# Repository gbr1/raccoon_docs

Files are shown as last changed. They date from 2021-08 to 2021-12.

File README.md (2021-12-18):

# Documentation and "how to" of UP Raccoon robot



# 

UP Raccoon is an AMR designed in collaboration with AAEON - UP.  This robot is completely opensource and easy to build.

## Software

Check this [guide](Raccoon&#32;robot&#32;setup.md)

## Assembly

Check the [manual assembly](assembly_manual/0_bill_of_materials.md)

## Learn more

Check these [diagrams](Raccoon&#32;robot&#32;diagrams.md)

## Events

Maker Faire Rome live [video](https://www.youtube.com/watch?v=H5PWxFA-pxc) (ita/eng)

## Demo

Check this [guide](./demo_units_docs/How%20to%20use%20the%20demo.md)

---

> ***Copyright © 2021 G. Bruno gbr1.github.io under MIT license***

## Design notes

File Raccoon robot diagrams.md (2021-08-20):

# Raccoon robot diagrams

## Hardware

Robot works on a 3S LiPo battery.

Following is how devices are powered.

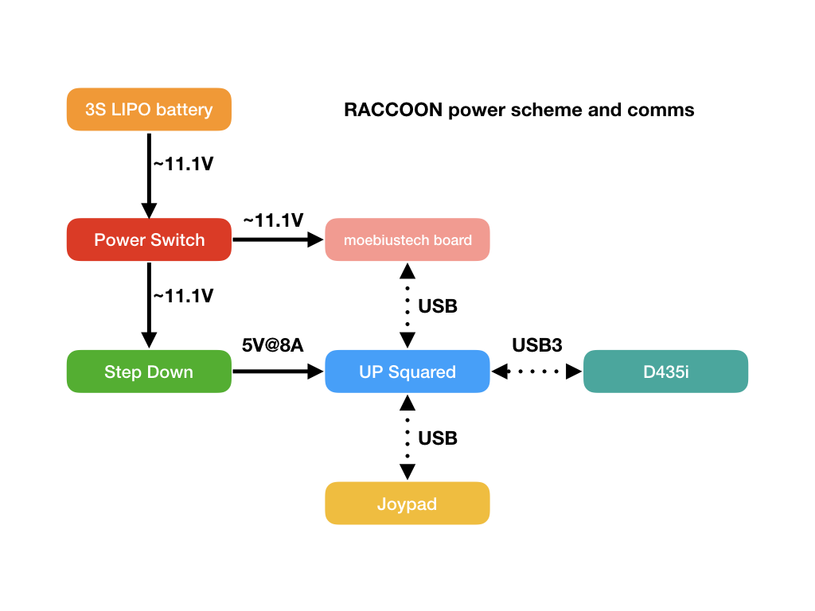
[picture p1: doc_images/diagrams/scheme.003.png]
power scheme Power diagram


## Software

The demo version works on ROS1. Check the following diagrams to take a look at involved nodes and packages.

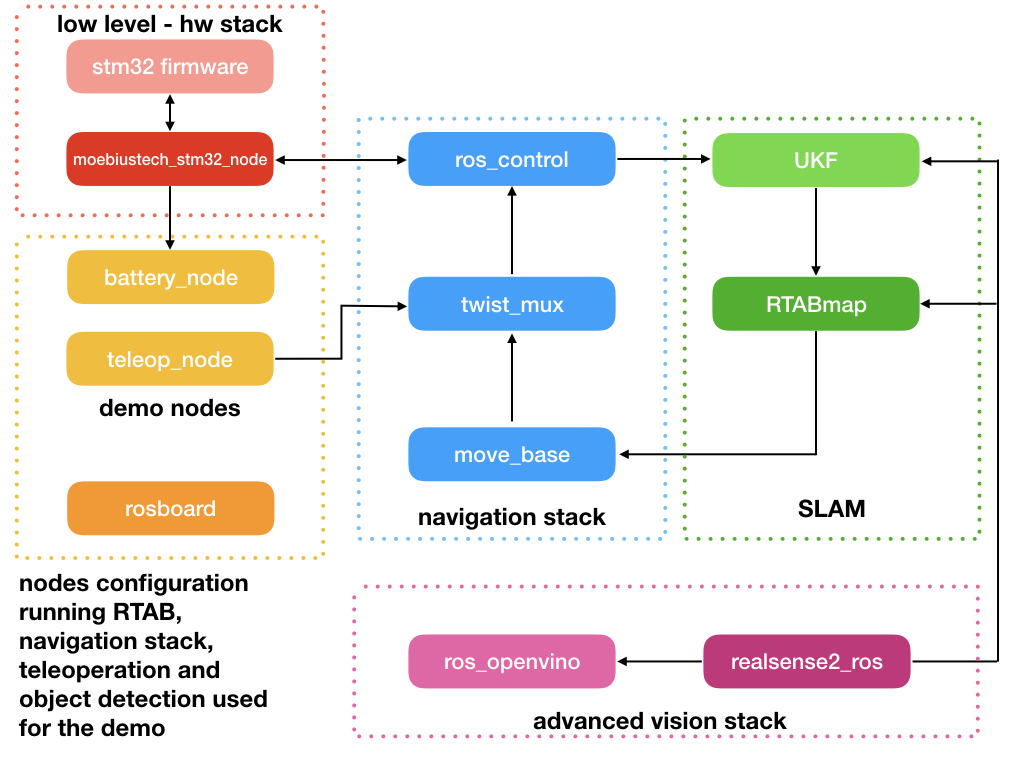
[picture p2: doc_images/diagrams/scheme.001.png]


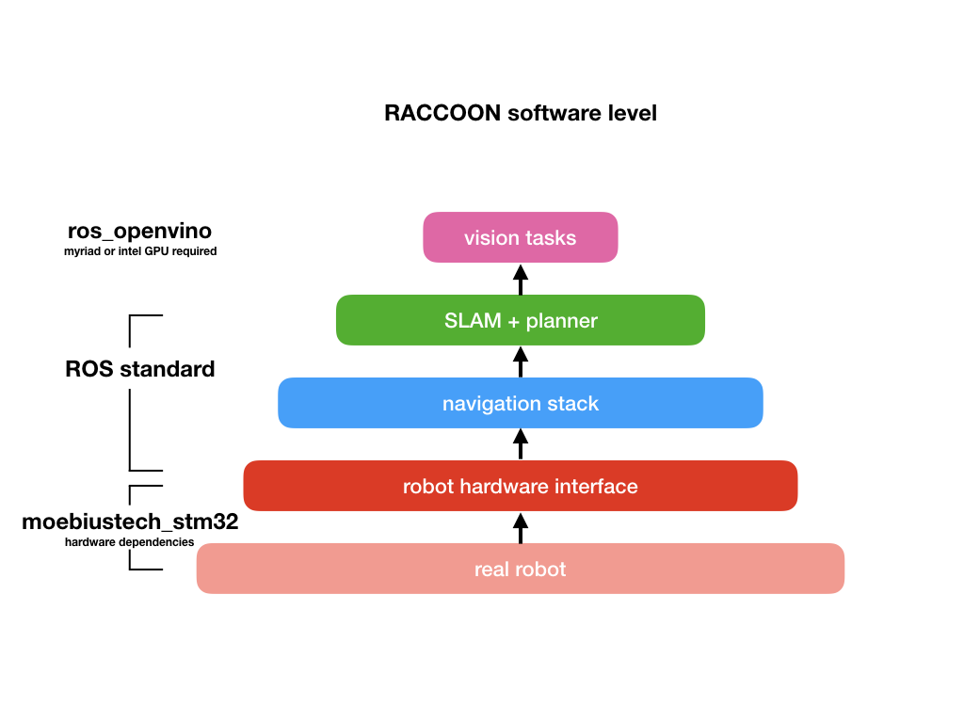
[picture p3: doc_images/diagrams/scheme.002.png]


> ***Copyright © 2021 G. Bruno gbr1.github.io under MIT license***

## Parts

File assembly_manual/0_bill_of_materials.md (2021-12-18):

# Bill of Materials

# 

### 1. Electronics & Electromechanicals

| id  | Part | Description | Qty |
| --- | --- | --- | --- |
| E01 | AAEON UP2 | UP Squared sbc | 1 |
| E02 | Wifi kit | WiFi card with antennas (PCB+SMA) | 1 |
| E03 | AAEON AI Core X | Myriad X module in PCI-e format | 1 |
| E04 | Moebiustech STM32 rosboard | A ROS board based on STM32F103RC | 1 |
| E05 | DCDC | A buck converter that can power UP2 from 12V | 1 |
| E06 | Intel Realsense D435i | Intel Realsense D435i | 1 |
| E07 | Gearmotor JGB37-520 | 12V 30:1 Gearmotor with encoder | 2 |
| E08 | Gearmotor cable | Gearmotor cable with JST connectors | 2 |
| E09 | Power switch | A round switch with red/black cables | 1 |
| E10 | Power Jack | 5.5-2.1 jack with 25cm red/black cable | 1 |
| E11 | 22AWG Cable | A 50cm red/black cable | 1 |
| E12 | USB C cable | USB 3.0 <-> USB C cable | 1 |
| E13 | USB micro cable | USB 2.0 <-> micro USB cable | 1 |
| E14 | DEANS cable | a red/black cable with DEANS connector | 1 |
| E15 | Mammoth connector | 3 vias mammout connector (3 vias) | 1 |

### 2. Mechanicals

| id  | Part | Description | Qty |
| --- | --- | --- | --- |
| M01 | M2.5x20+6 | Standoffs with M2.5 mounts, 20mm with 6mm screw | 4 |
| M02 | M3x30+6 | Standoffs with M3 mounts, 30mm with 6mm screw | 4 |
| M03 | M2.5 nut | M2.5 nuts | 22  |
| M04 | M3 nut | M3 nuts | 12  |
| M05 | M2.5x6 | M2.5 screw of 6mm lenght | 18  |
| M06 | M2.5x14 | M2.5 screw of 14mm lenght | 4 |
| M07 | M3x5 | M3 screw of 5mm lenght | 12  |
| M08 | M3x10 | M3 screw of 10mm lenght | 16  |
| M09 | Cable tie | a cable tie | 1 |
| M10 | Gearmotor bracket | A "L" bracket needed to mount a gearmotor on a plate | 2 |
| M11 | Wheel 65mm | 65mm wheel with a 6mm hole | 2 |
| M12 | Magnet ⌀10x3 | Neodimium magnet (diameter 10mm and height 3mm) with N/S polarized faces | 4 |
| M13 | Caster wheel | 1inch caster wheel | 1 |

### 3. 3D Printable

| id  | Part | Description | Qty |
| --- | --- | --- | --- |
| P01 | Bottom plate | Bottom plate of the robot | 1 |
| P02 | Top plate | Top layer of the robot | 1 |
| P03 | Battery bracket | An optional magnetic bracket needed to fix the battery | 1 |
| P04 | Moebiustech Board spacer | A spacer needed to mount the E04 (Moebiustech STM32) component | 1 |
| P05 | DCDC spacer | A spacer needed to mount the E05 (DCDC) component | 1 |

For 3d printable you can use [this guide](../3d_print/readme.md).

---

## Start building your UP Raccoon

[Go to the UP Squared setup](1_UP_Squared_setup.md)

---

> ***Copyright © 2021 G. Bruno gbr1.github.io under MIT license***

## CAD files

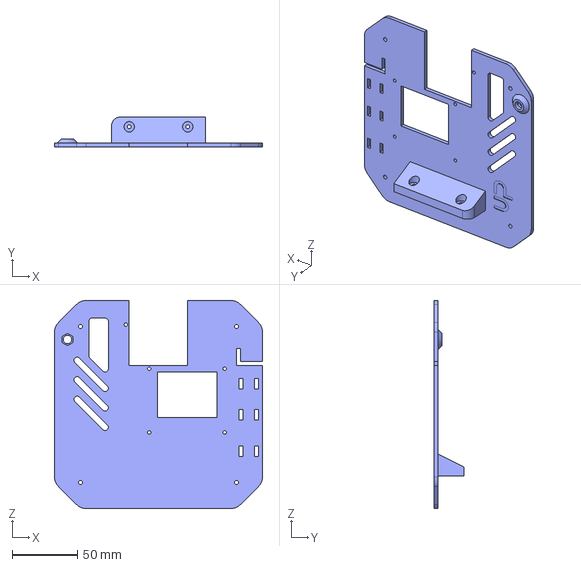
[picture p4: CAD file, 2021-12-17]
3d_print/step/top_plate.step
160.0 x 23.0 x 160.0 mm

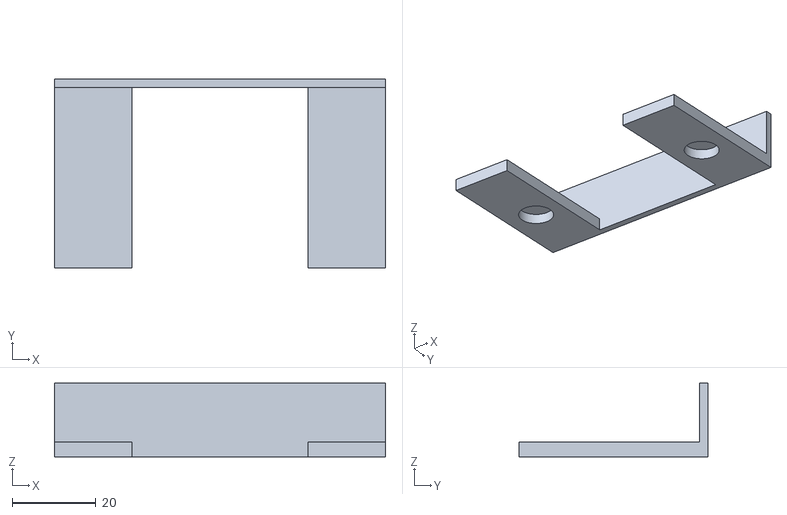
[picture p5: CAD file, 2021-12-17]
3d_print/stl/battery_cover.stl
79.0 x 45.0 x 17.6

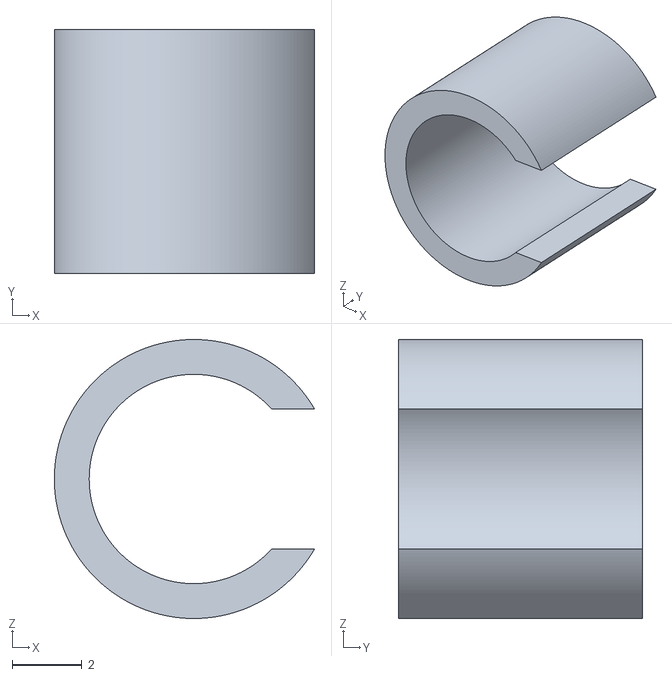
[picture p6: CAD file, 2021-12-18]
demo_units_docs/files/adapter v1.stl
7.46 x 7.00 x 8.00

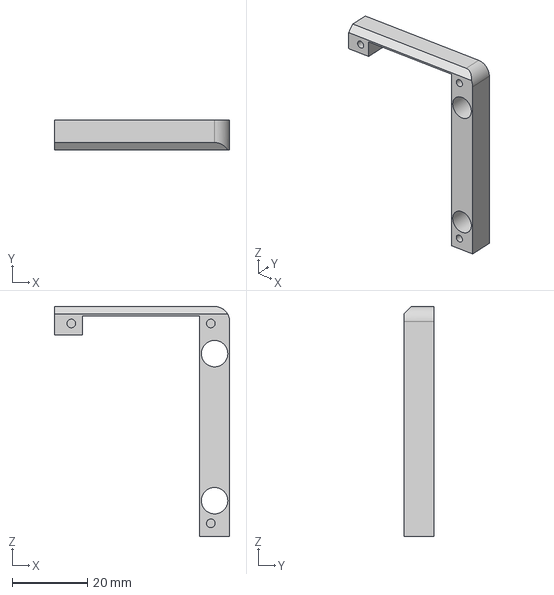
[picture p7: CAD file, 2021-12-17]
3d_print/step/dcdc_spacer.step
46.5 x 8.00 x 61.0 mm

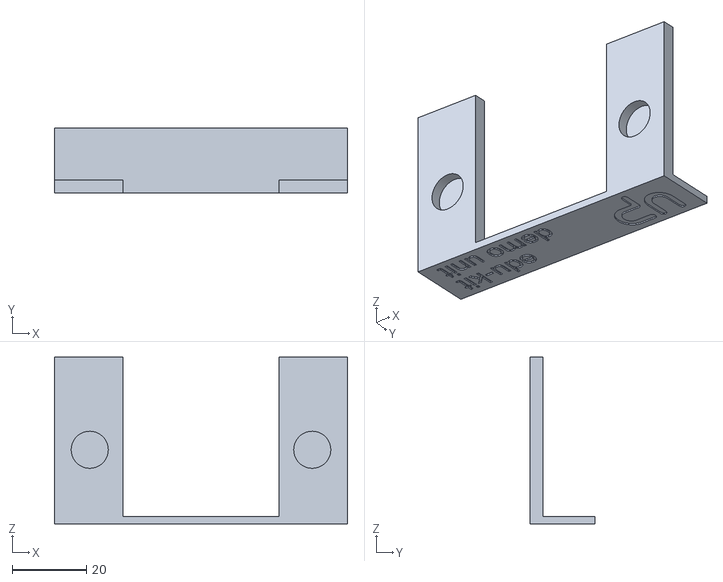
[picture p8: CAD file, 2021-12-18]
demo_units_docs/files/battery_cover_edukit_demo v4.stl
79.0 x 17.6 x 45.0

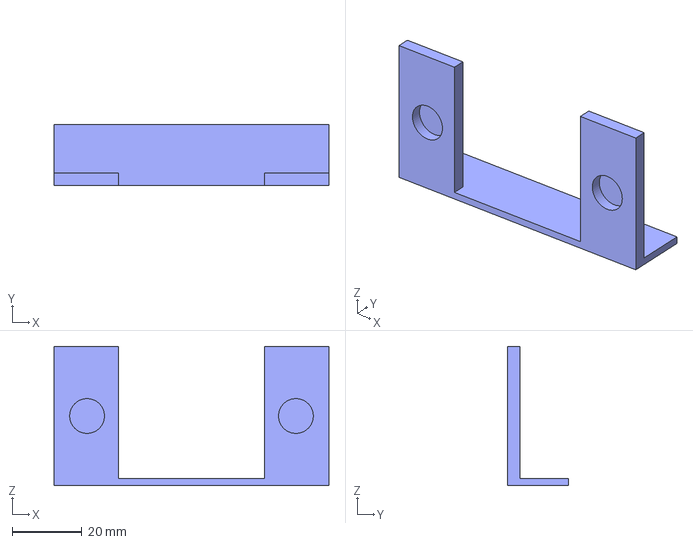
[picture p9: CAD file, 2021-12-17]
3d_print/step/battery_cover v3.step
79.0 x 17.6 x 40.0 mm

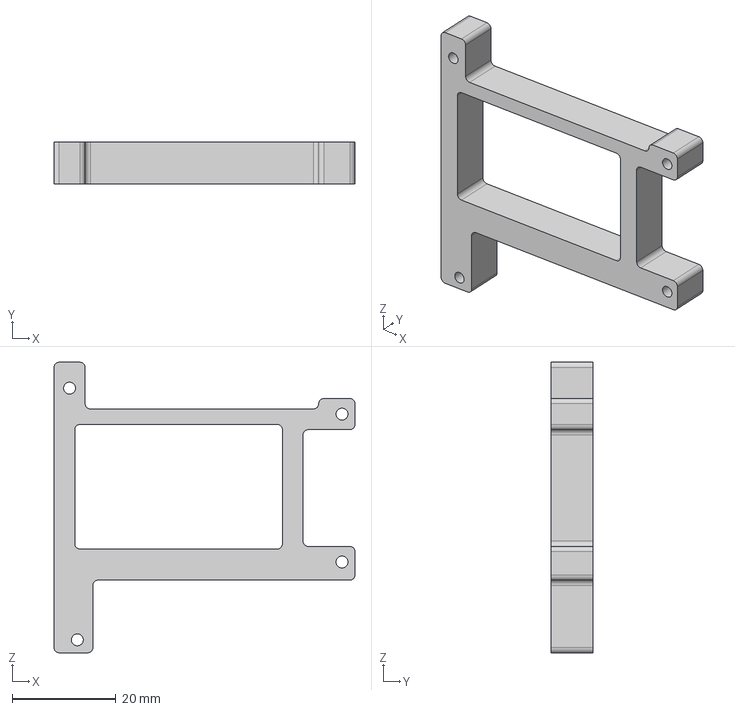
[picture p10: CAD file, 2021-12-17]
3d_print/step/moebius_spacer.step
58.0 x 8.00 x 56.0 mm

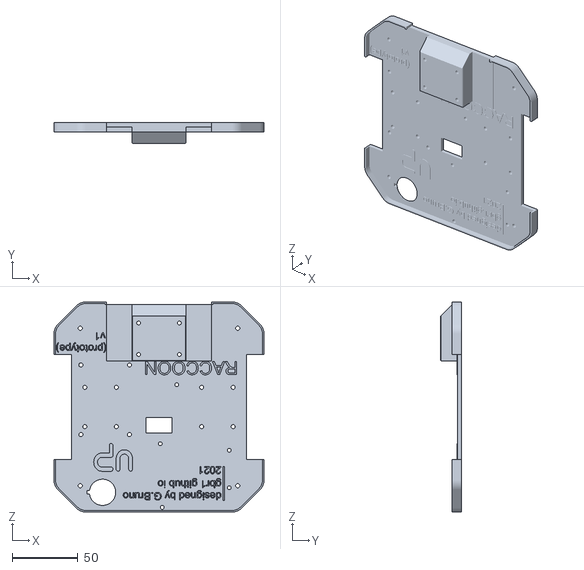
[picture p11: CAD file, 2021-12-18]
demo_units_docs/files/plate_01 v24.stl
160.0 x 16.0 x 160.0

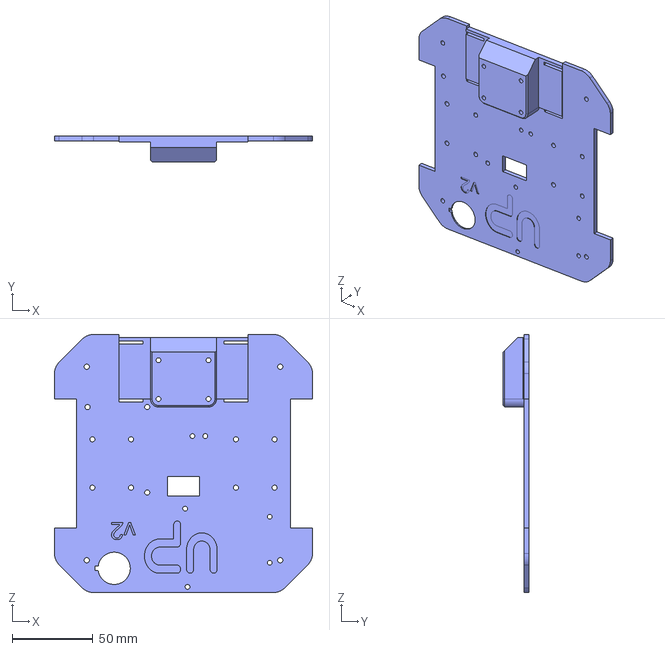
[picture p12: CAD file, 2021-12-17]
3d_print/step/bottom_plate.step
160.0 x 16.0 x 160.0 mm

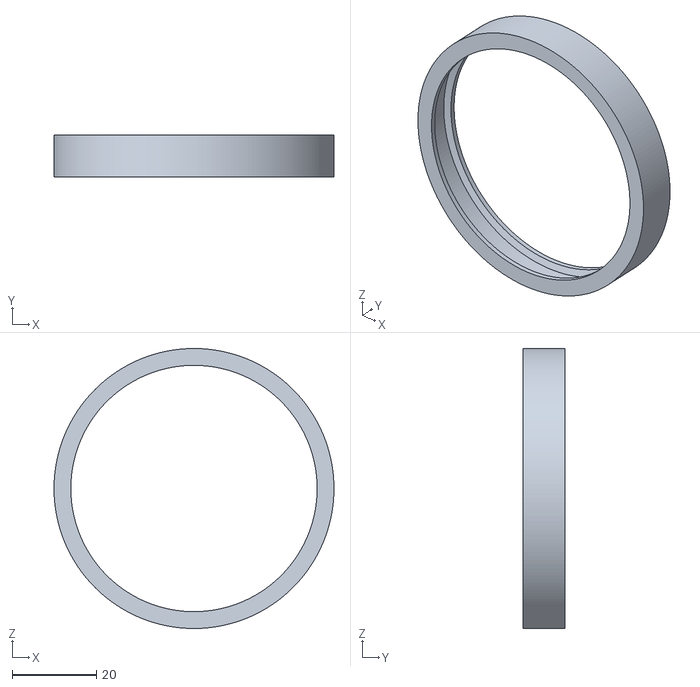
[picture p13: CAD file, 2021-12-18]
demo_units_docs/files/tyre v1.stl
66.4 x 10.0 x 66.4

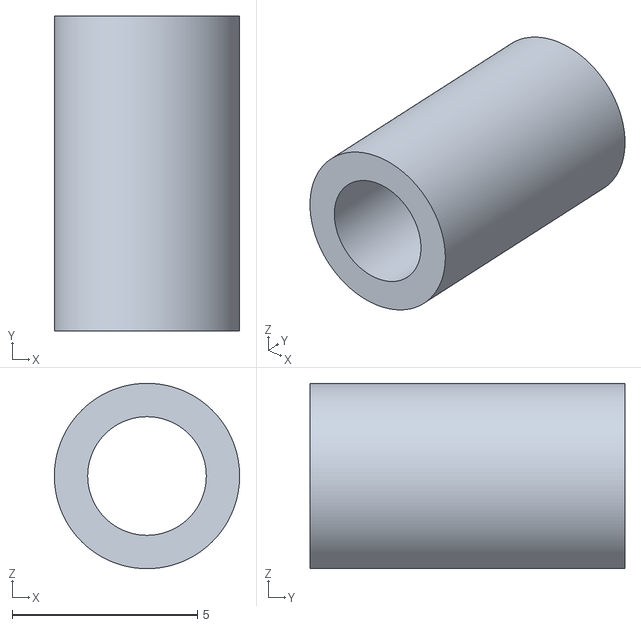
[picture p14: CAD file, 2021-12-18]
demo_units_docs/files/battery_screw v1.stl
5.00 x 8.50 x 5.00

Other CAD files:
demo_units_docs/files/plate_02 v20.stl
3d_print/stl/bottom_plate.stl
3d_print/stl/dcdc_spacer.stl
3d_print/stl/moebius_spacer.stl
3d_print/stl/top_plate.stl

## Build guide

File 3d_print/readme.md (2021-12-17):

# 3D printing instructions

# 

You can get 3D files in STL format [here](./stl)

If you want to edit files, you can use [STEP files](./step) and import into your favourite CAD.

## bottom_plate *P01* ([file](./stl/bottom_plate.stl))

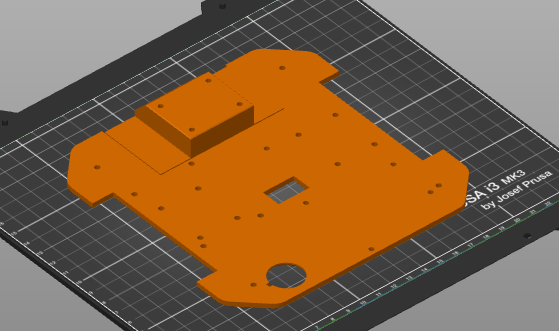
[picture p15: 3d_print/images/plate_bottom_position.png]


* top/bottom: 3 layers
* perimeters 1.2mm
* 0.4 extruder
* 0.2 z resolution
* no supports
* 10% infill
* grid infill

NOTE: It should be not an issue print holes in the bottom center area (caster mount) without supports.

## top_plate *P02* ([file](./stl/top_plate.stl))

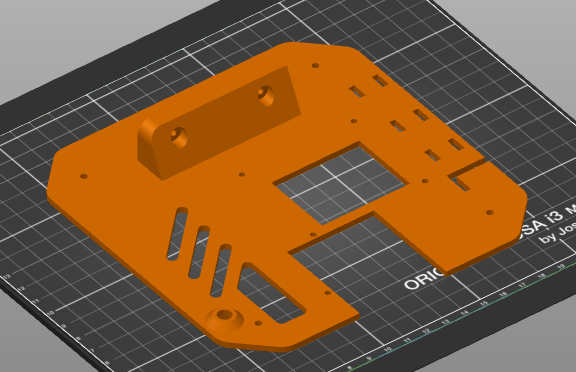
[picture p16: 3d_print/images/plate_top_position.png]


* top/bottom: 3 layers
* perimeters 1.2mm
* 0.4 extruder
* 0.2 z resolution
* no supports
* 10% infill
* grid infill

NOTE: It should be not an issue print the hole in the bottom left area (antenna mount) without supports.

## battery_cover *P03* ([file](./stl/battery_cover.stl))

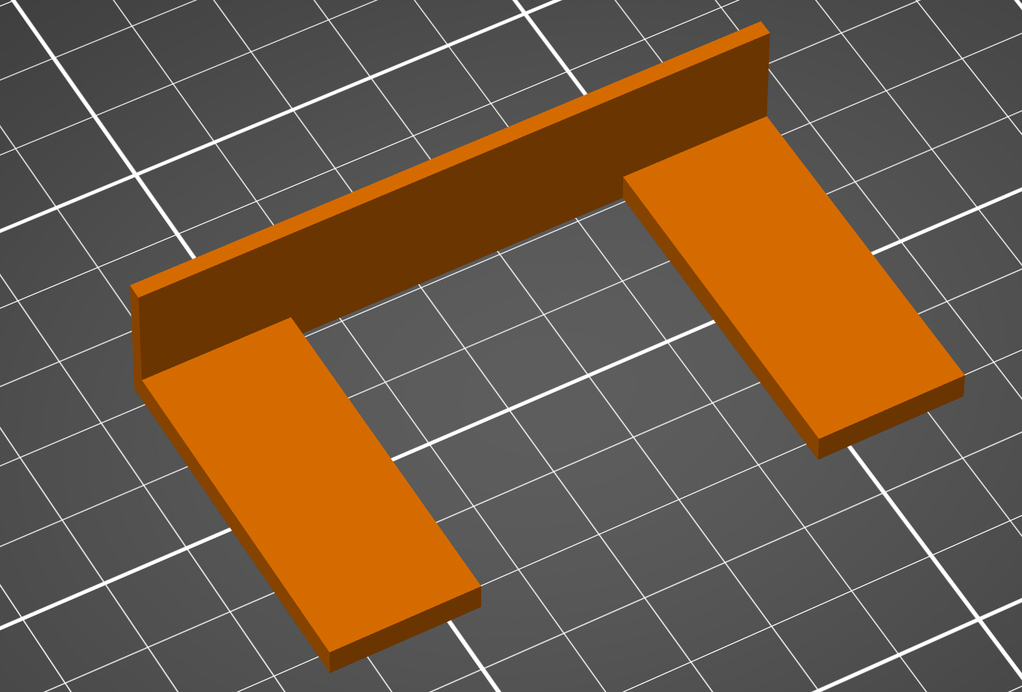
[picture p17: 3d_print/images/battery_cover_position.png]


* top/bottom: 3 layers
* perimeters 1.2mm
* 0.4 extruder
* 0.2 z resolution
* no supports
* 10% infill
* grid infill

## moebiustech_spacer *P04* ([file](./stl/moebiustech_spacer.stl))

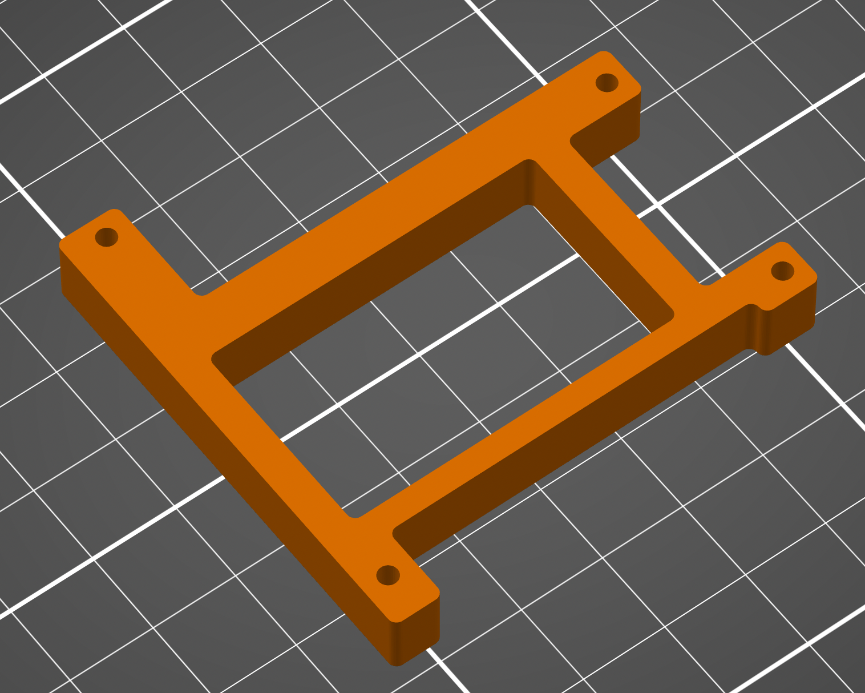
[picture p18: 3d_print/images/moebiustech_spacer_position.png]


* top/bottom: 3 layers
* perimeters 1.2mm
* 0.4 extruder
* 0.2 z resolution
* no supports
* 20% infill
* grid infill

## dcdc_spacer *P05* ([file](./stl/dcdc_spacer.stl))

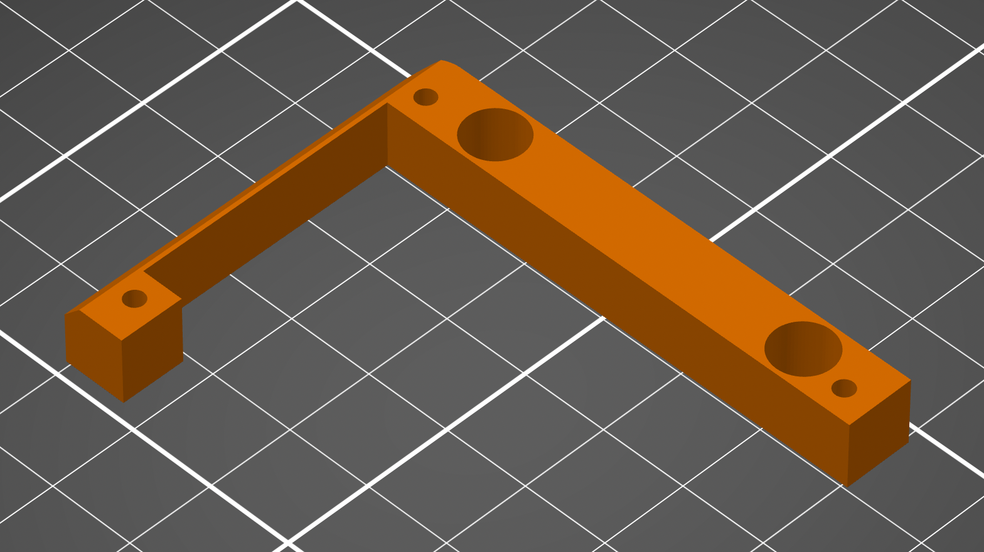
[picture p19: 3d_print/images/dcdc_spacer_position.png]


* top/bottom: 3 layers
* perimeters 1.2mm
* 0.4 extruder
* 0.2 z resolution
* no supports
* 20% infill
* grid infill

---

> ***Copyright © 2021 G. Bruno gbr1.github.io under MIT license***

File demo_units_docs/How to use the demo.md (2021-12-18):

# How to use the demo

---

## 1.  Insert battery

Firstly you need to insert the battery.

Detach the magnetic bracket on the back of the robot.

Insert the battery, reattach the magnetic bracket and connect the DEANS connector.

## 2. Turn on

Check if the switch on Moebiustech board in turned on and turn on the switch on the bottom of the robot

You will see turning on:

- a red light on the Moebiustech board;

- a blue light for each motor

- a blue light on the back of the UP Squared

- a green light from the AI Core X (internal part of the robot)

- a little green light from the DC/DC

Now you have to wait that a blue light over the ethernet connector of UP Squared is turned on.

## 3.  Start the demo

When the robot is ready a blue light over the ethernet connector of UP Squared is turned on.

Automatically after about 1 second another light will turn on (it could be Red, Yellow or Green) that represent the battery state. Check the battery section of this guide to learn more.

Bring your smartphone, tablet or computer and check for a WiFi network called "raccoon-robot". Connect to this network by usign *robotdemo* password. 

In your favorite browser go to ***demo.local:8888*** and ROSBoard interface will appear.

## 4.  Use the demo

Press the menu button (the one with 3 lines) od ROSBoard and choose all topics you want to show.

If you always use the same device data will stored into your browser (check [saving already done configuration so that we cannot add everything again and again · Issue #76 · dheera/rosboard · GitHub](https://github.com/dheera/rosboard/issues/76))

Bring the joypad and press the central button (you will see a blue light on left).

Here a description of the controls:

- START: reset RTABmap

- B+left analog stick: move the robot at low speed (good to show SLAM)

- A+left analog stick: move the robot at medium speed

- X+left analog stick: move the robot at high speed (good to show how fast it is)

- SELECT+START+L+R: turn off

## 5.  Turn off

To turn off press SELECT+START+L+R simultaneously when joypad is connected.

Wait a while, you will see the power indicator on the UP Squared (the blue led on back right) turning off.

After that, turn off the general power switch on the bottom.

Detach the battery for security.

---

## Battery

When ROS is running on every second is published a topic */moebiustech_stm32/status* that contains the voltage value of the battery.

The battery_node in demo package shows on UP Squared leds the value of the battery. The color scheme is the following:

- GREEN, voltage ≥ 10.9V

- YELLOW, voltage ≥ 10.4V

- RED, voltage ≥ 10.2V

This node will turn off the UP Squared when 10.0V are reached as security mode.

To charge battery, detach from the robot connect to charger and select LIPO BALANCE 3S 1.8A program.

## Useful topics

- /camera/image_raw is the Realsense RGB sensor

- /camera/pointcloud/color is the Realsense pointcloud (enabled for the demo)

- /object_detection/image_raw is the mobilenetSSD view

- /rtabmap/cloud_map is the point cloud of the 3D environment that robot is learning

- /rtabmap/grip_map is the 2D projected map from the 3D SLAM

- /moebiustech_stm32/status is battery voltage

- /odometry/filtered is the UKF result of various odometry sources (visual odometry+wheels odometry)

- /dmesg if there are some errors.

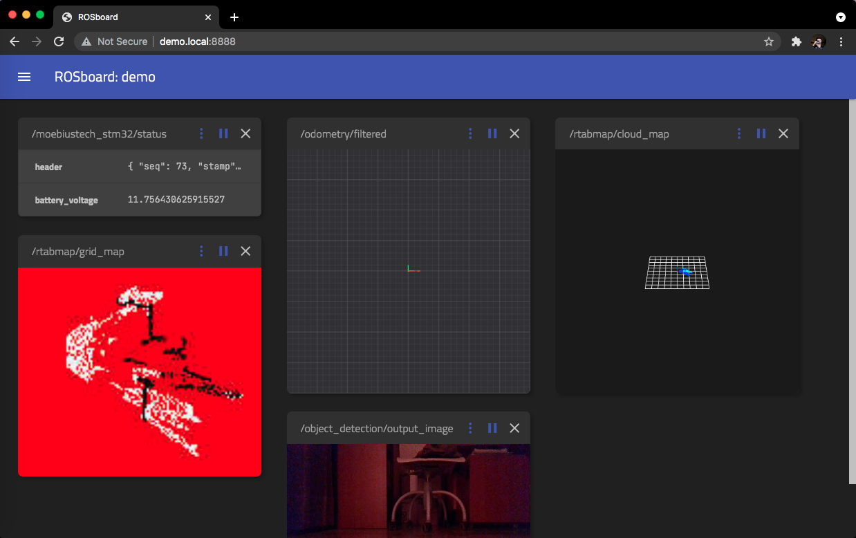
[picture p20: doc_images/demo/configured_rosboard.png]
rosboard ROSBoard full configuration


---

## Troubleshooting

- If your robot turns off immediately:
  
  1. check battery voltage
  
  2. check if Moebiustech board is turned on

- If your robot can't be controller by joypad:
  
  1. check the manual of the joypad
  
  2. check if your joypad is in X mode
  
  3. check if your joypad is charged
  
  4. if you see only lag, wait a while and then retry. If persist check UP Squared temperature

- If object detection topic is absent or not work you must restart the robot (known issue of NCS2/Myriad X by Intel)

If you still encounter issues please send an email to [giovannididio.bruno@gmail.com](giovannididio.bruno@gmail.com)

> ***Copyright © 2021 G. Bruno gbr1.github.io under MIT license***

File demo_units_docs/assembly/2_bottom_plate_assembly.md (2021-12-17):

# Bottom plate setup

1. Fit 2 magnets into the 3d printed battery holder

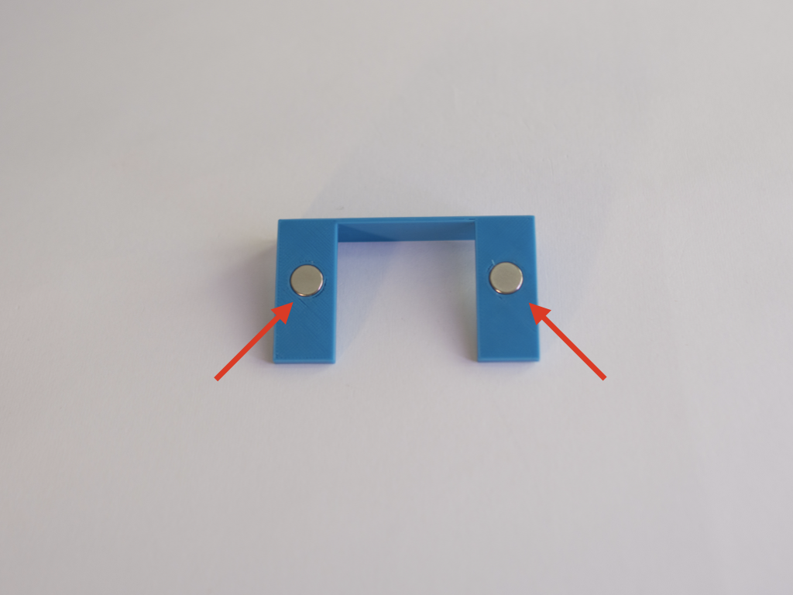
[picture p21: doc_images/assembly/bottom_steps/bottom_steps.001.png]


2. Using the maded part check the correct orientation of the magnets to be mounted into the 3d printed bottom plate

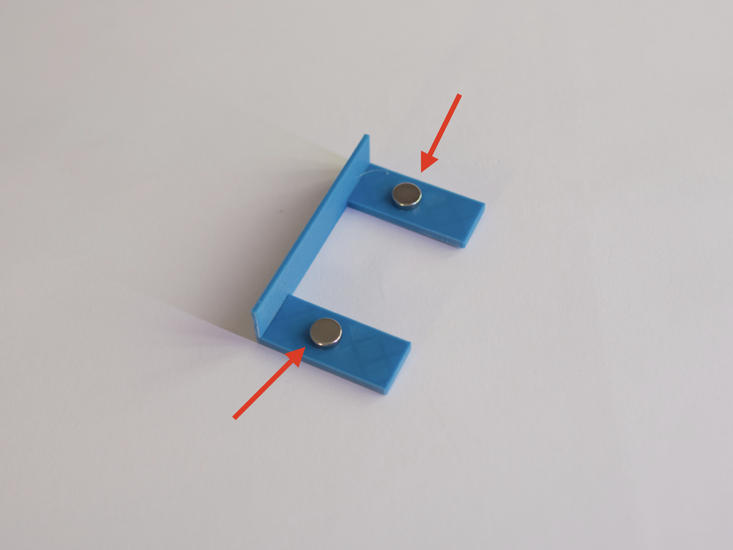
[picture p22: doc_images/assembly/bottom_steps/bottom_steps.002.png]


3. Mount the magnets into the bottom plate

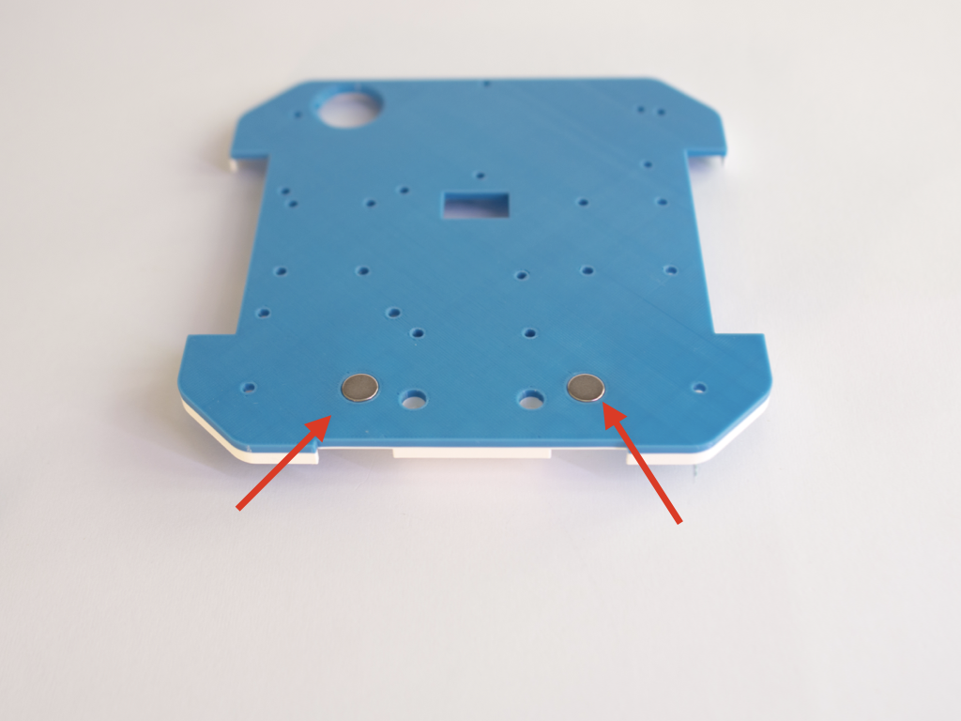
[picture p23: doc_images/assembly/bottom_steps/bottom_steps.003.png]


4. Check if everything is mounted correctly

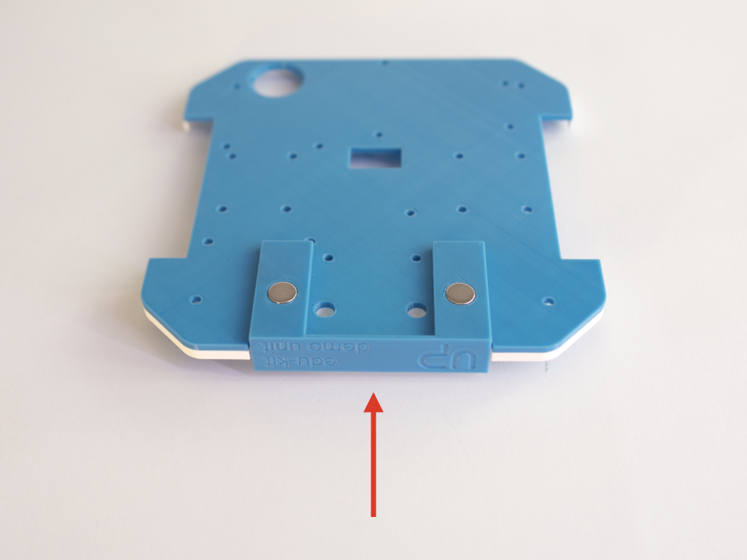
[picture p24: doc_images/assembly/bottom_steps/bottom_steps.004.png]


5. Bring 8 M3x6 screws, 8 M3 nuts and motor brackets

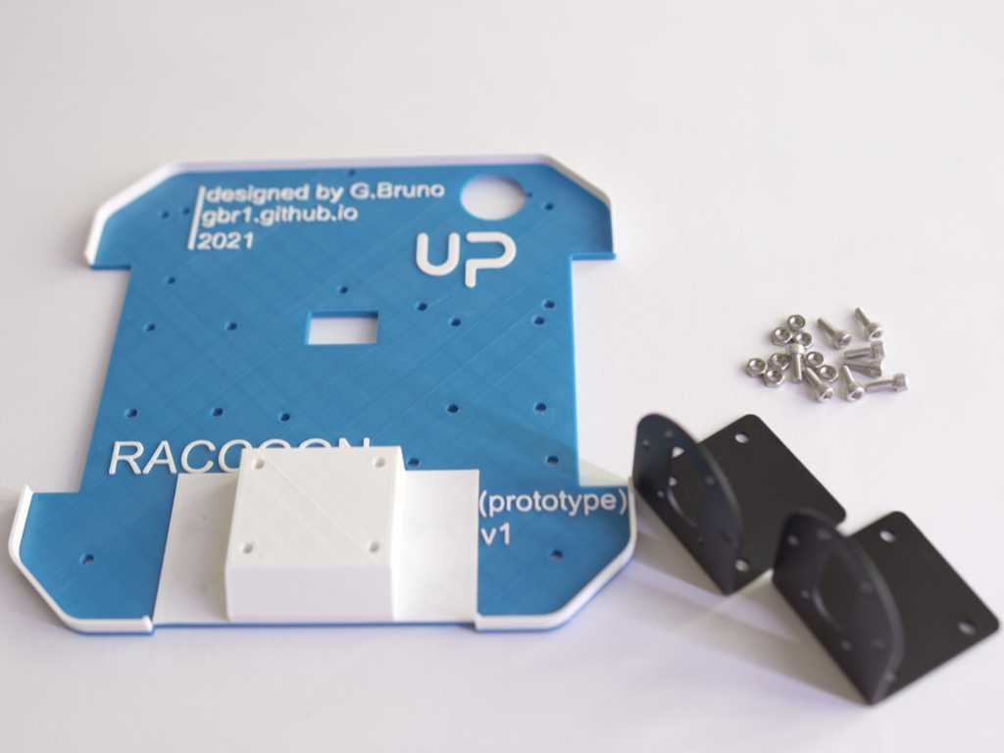
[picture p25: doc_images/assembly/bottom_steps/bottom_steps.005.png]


6. Start mounting the brackets as shown

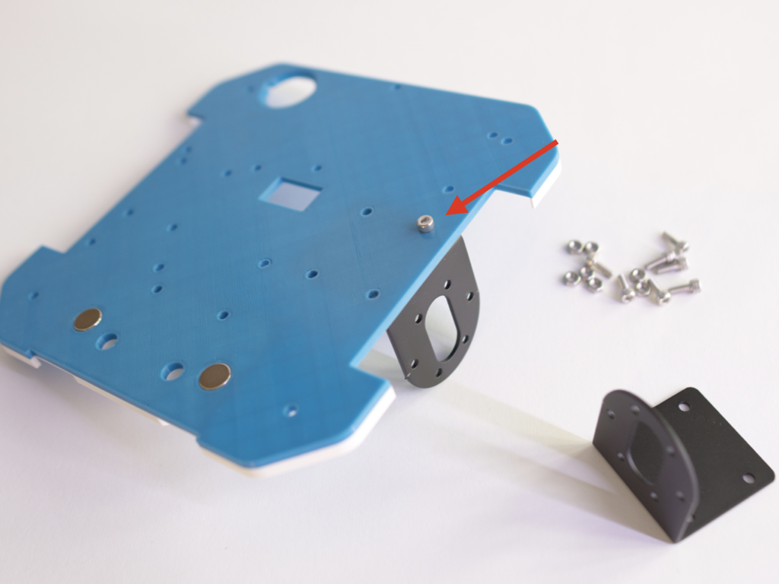
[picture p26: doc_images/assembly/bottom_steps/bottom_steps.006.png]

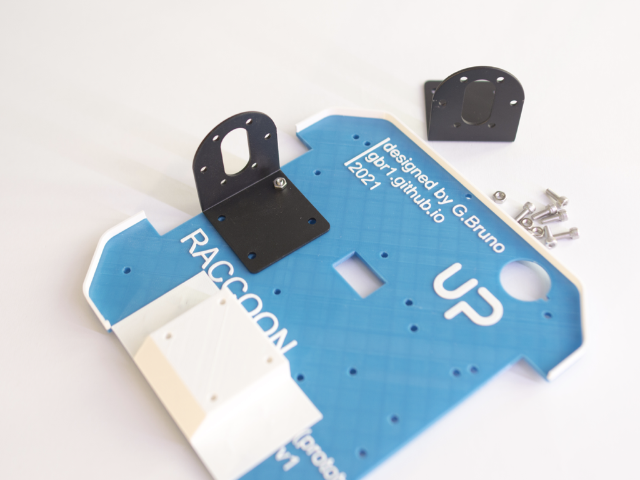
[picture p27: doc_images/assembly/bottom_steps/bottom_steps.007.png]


7. Mount all the screws and tight the nuts

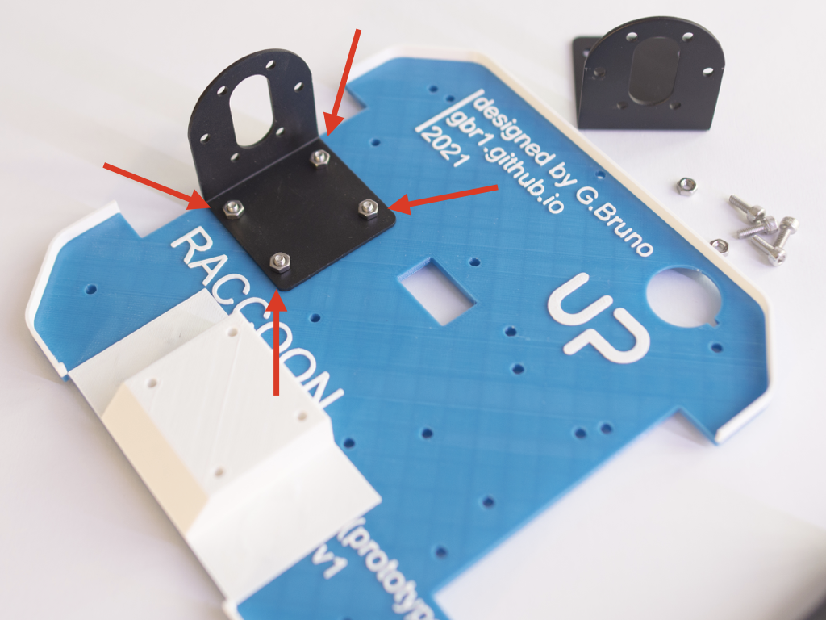
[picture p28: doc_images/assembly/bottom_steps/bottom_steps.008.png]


8. Mount the other bracket, too

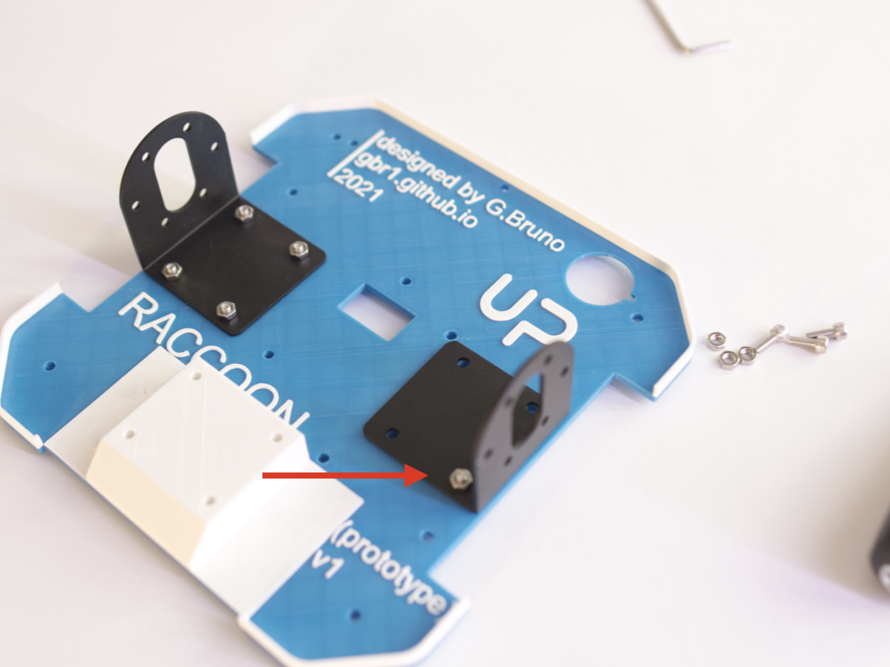
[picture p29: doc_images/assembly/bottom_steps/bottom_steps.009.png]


9. You should obtain something like the following photos

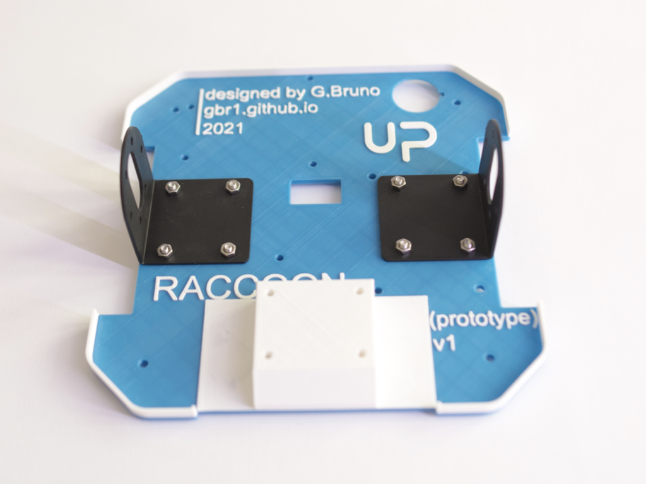
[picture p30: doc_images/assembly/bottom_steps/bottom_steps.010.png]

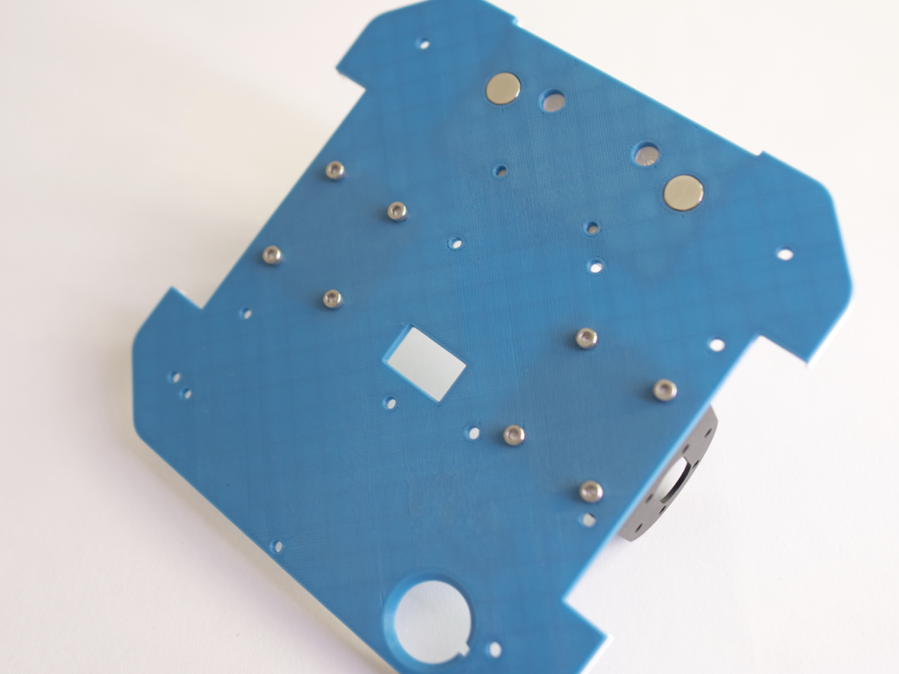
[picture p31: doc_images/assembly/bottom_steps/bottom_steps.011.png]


10. Bring 4 M2.5x5 standoffs and 4 M2.5 nuts

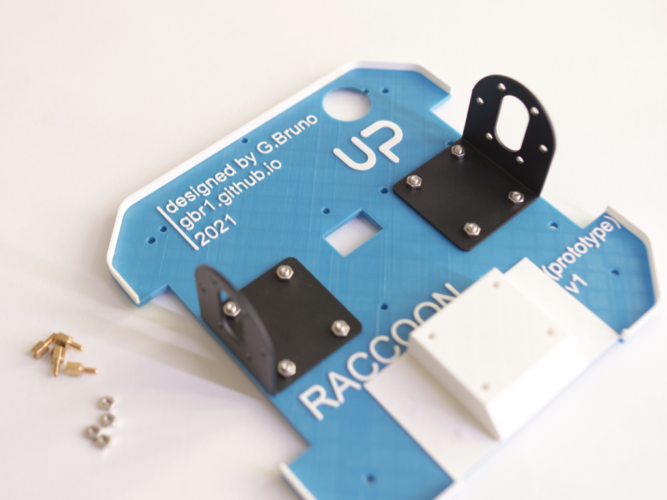
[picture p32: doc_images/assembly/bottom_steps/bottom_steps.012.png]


11. Place as shown

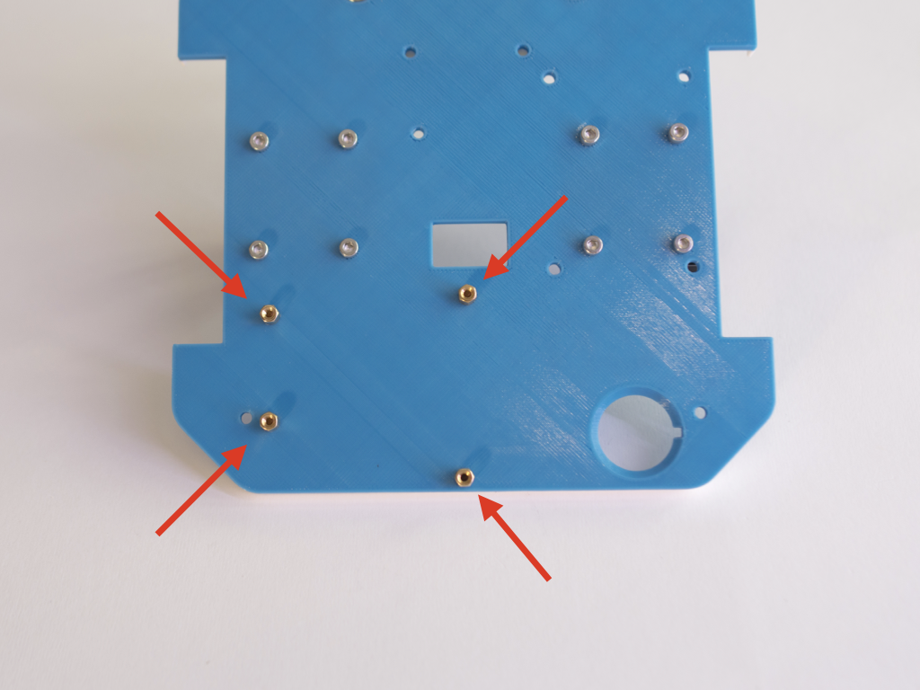
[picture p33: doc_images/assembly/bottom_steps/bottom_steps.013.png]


12. Fix with the nuts as shown

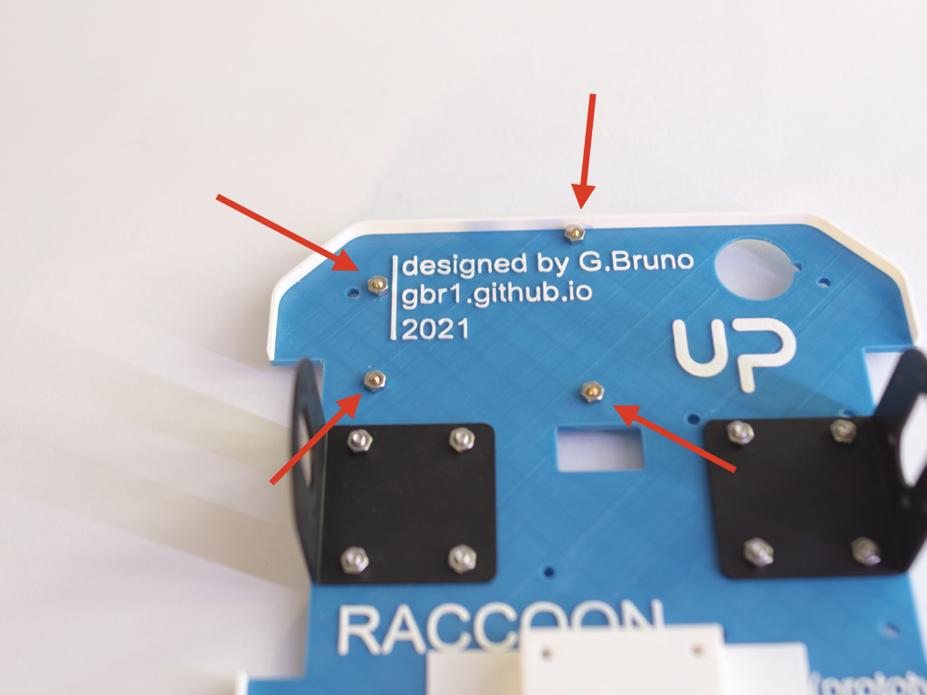
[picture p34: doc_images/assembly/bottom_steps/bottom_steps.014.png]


13. Bring 4 M2.5x6 standoffs and 4 M2.5 nuts

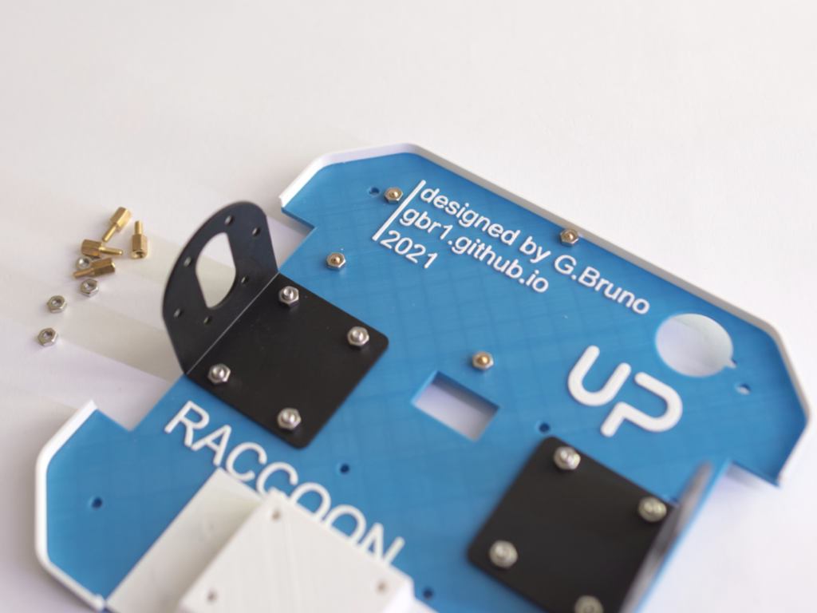
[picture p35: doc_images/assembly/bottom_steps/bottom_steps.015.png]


14. Place as shown

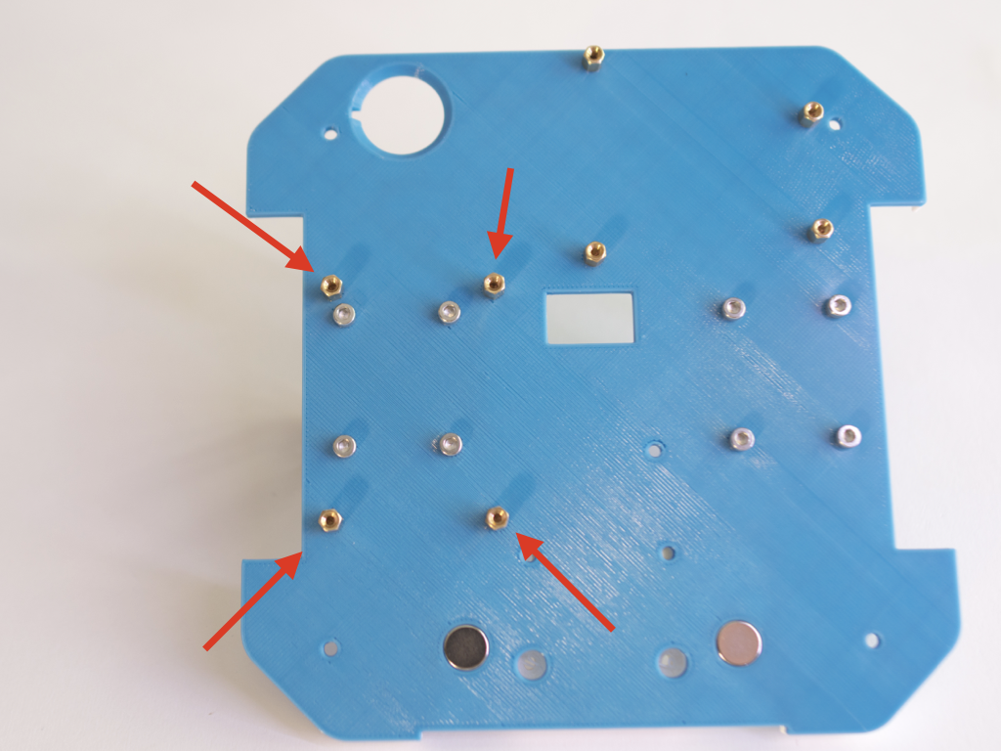
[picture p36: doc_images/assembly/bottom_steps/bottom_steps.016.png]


15. Fix with nuts

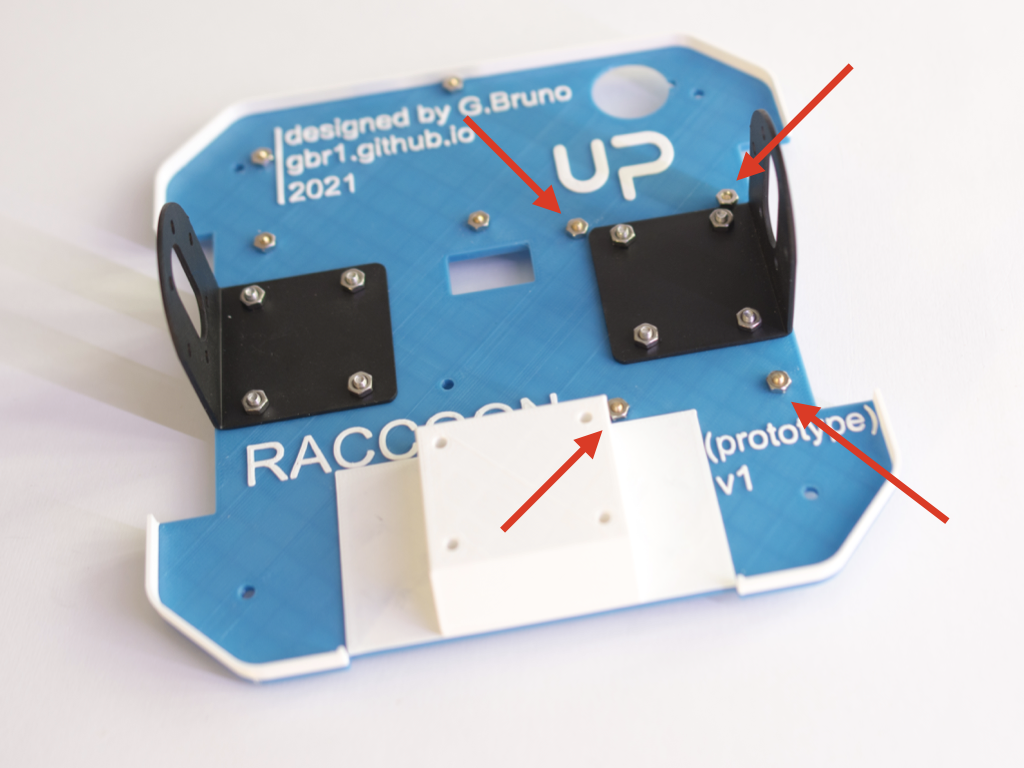
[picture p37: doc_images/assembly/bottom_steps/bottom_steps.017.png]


16. For next steps you need 2 M3x30 screws and 2 3d printed battery spacers

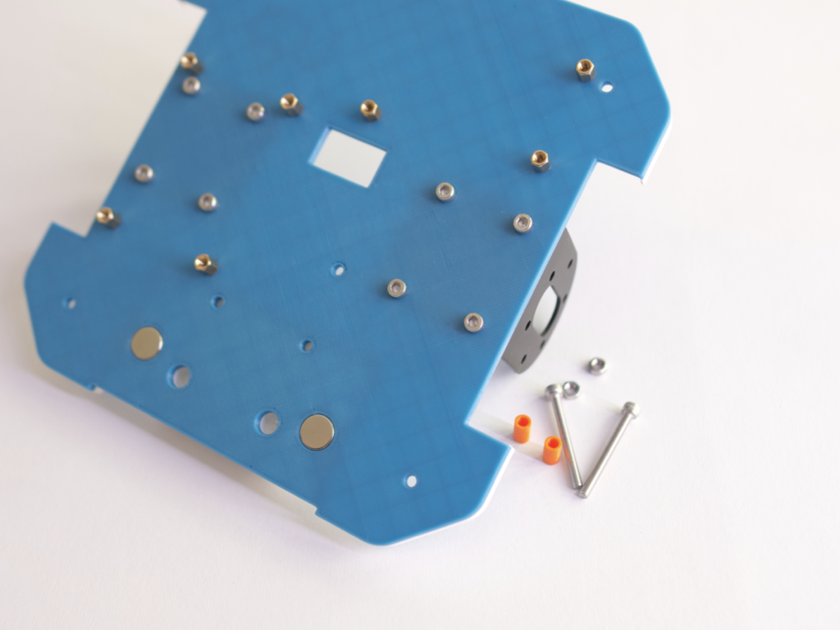
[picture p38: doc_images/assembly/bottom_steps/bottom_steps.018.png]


17. Insert the spacers into the screws

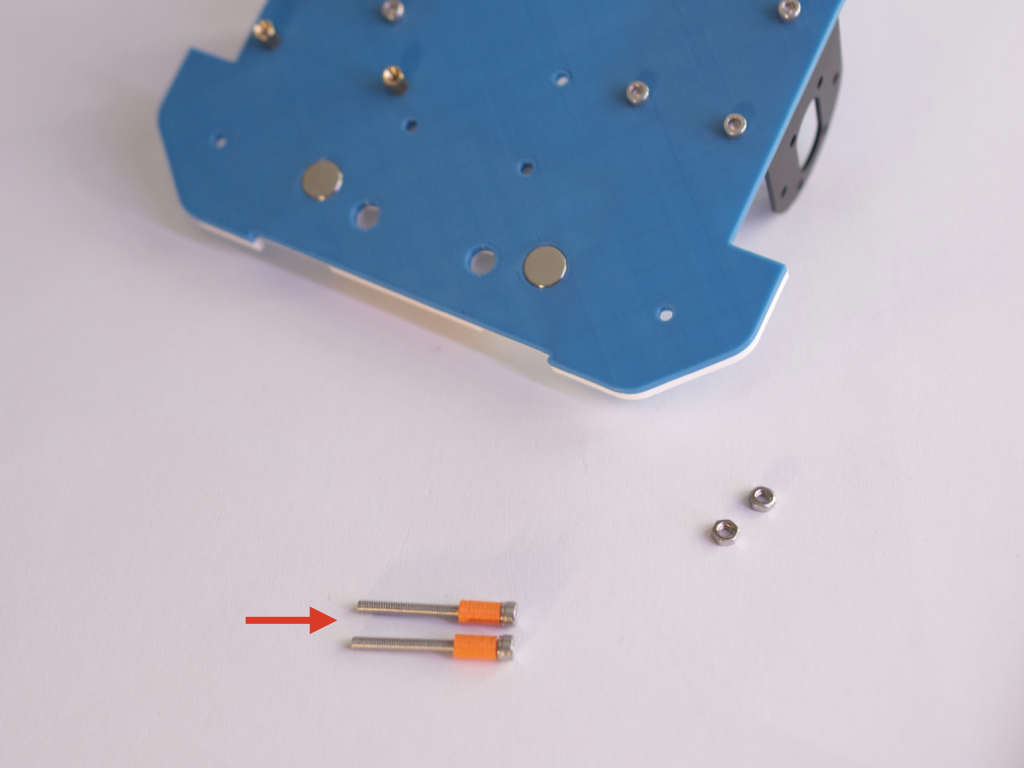
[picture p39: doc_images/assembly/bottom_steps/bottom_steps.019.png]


18. Screw the screws as shown

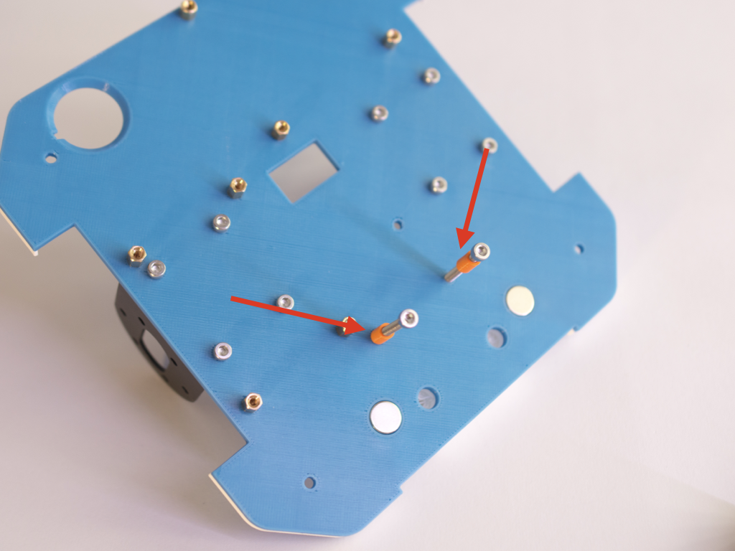
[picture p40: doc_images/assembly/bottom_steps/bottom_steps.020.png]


19. This is how it should appear

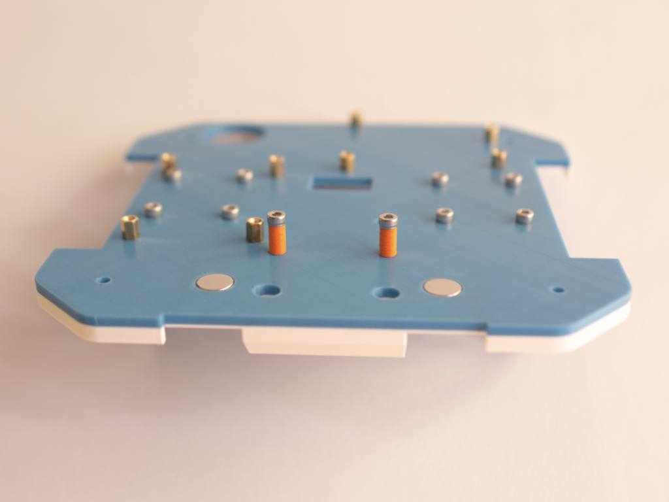
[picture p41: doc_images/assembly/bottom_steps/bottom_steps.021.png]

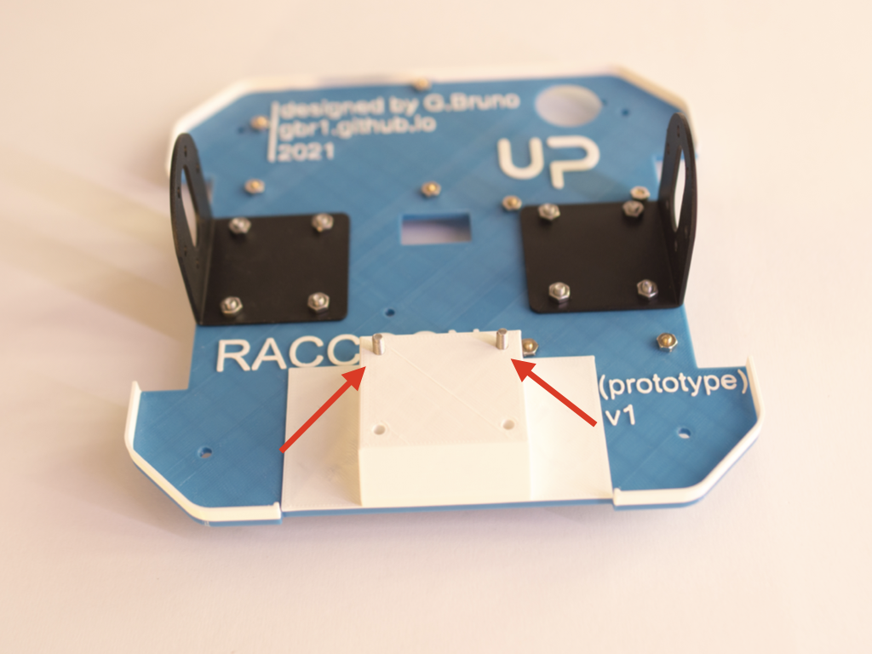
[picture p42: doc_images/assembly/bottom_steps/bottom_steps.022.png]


20. Bring 2 M3x14 screws, 4 M3 nuts and the caster wheel

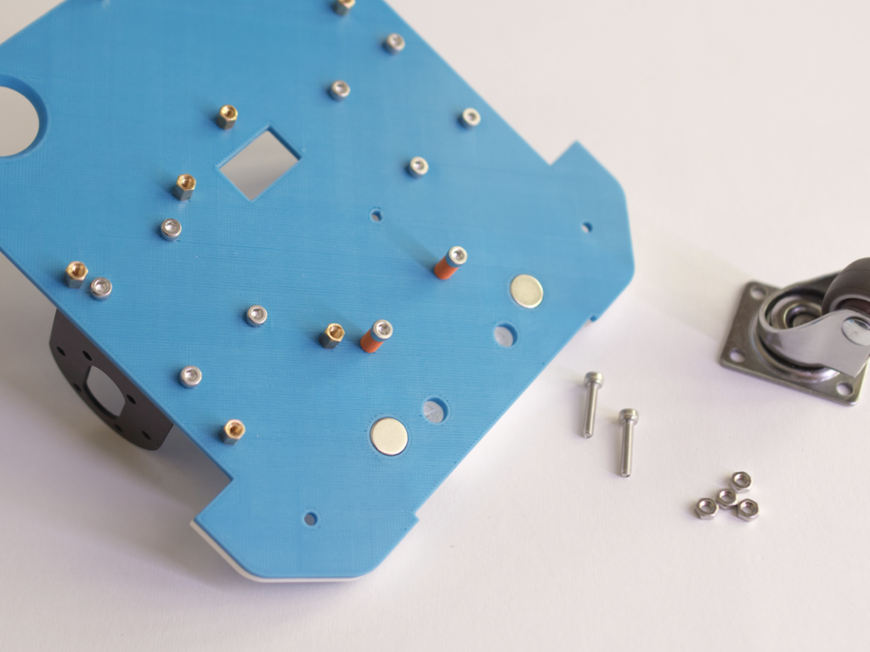
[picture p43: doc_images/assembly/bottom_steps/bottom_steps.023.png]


21. Place the screws as shown

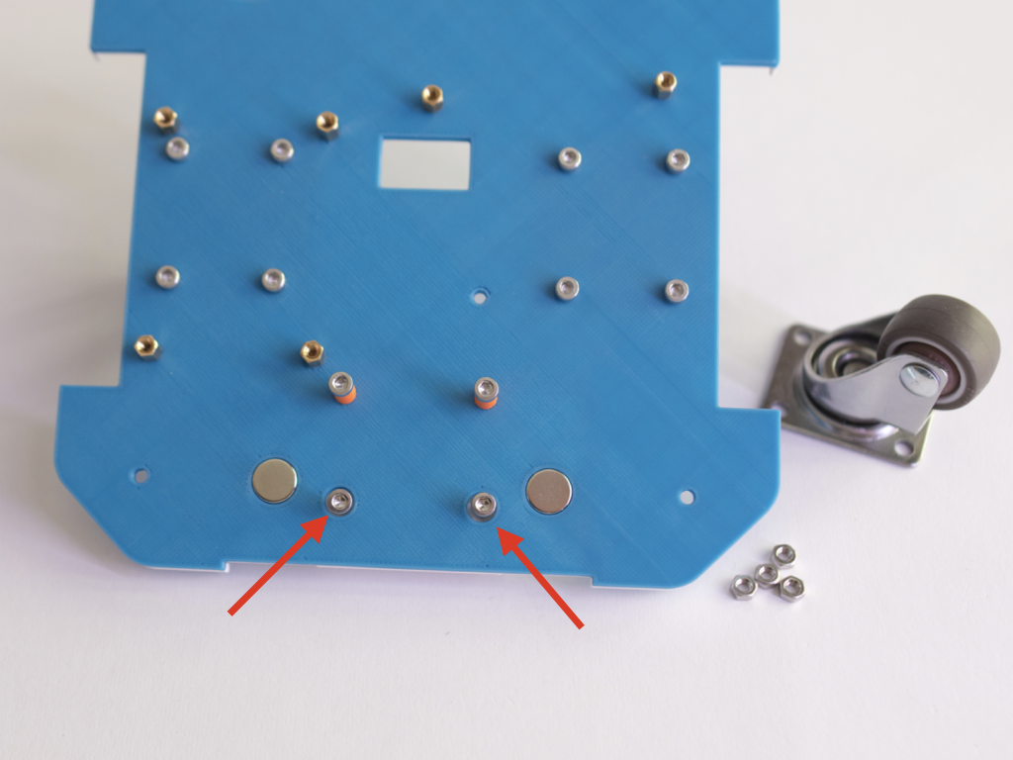
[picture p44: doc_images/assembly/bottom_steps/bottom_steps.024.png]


22. Screw until your part looks like the following photo 

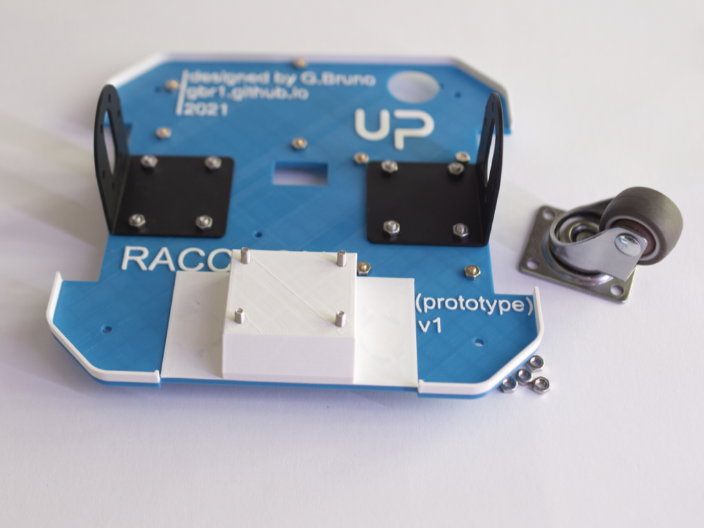
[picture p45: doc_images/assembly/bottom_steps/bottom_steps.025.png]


23. Mount the caster wheel and fix using nuts

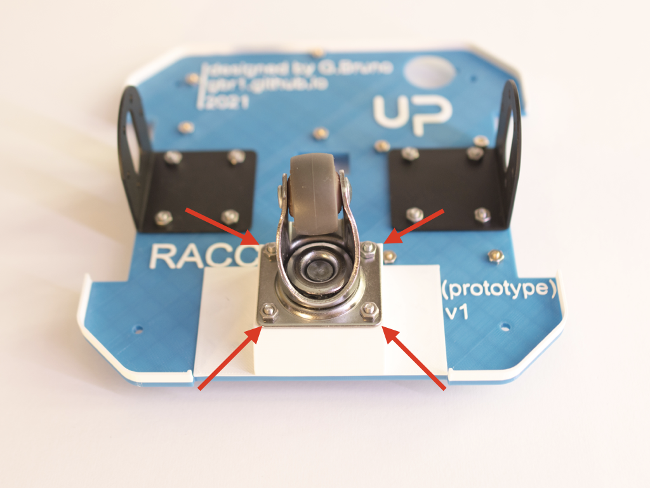
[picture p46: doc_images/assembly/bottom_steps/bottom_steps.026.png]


24. Now you need 2 motors and 12 M3x5 screws

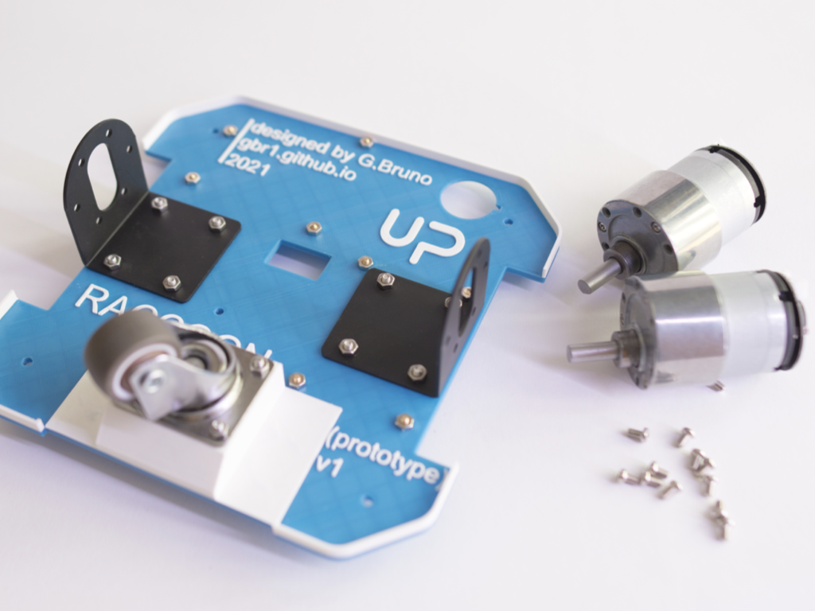
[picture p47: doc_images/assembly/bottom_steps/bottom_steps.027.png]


25. Place motor as shown in photo (it must be on top) an fix using 3 screws

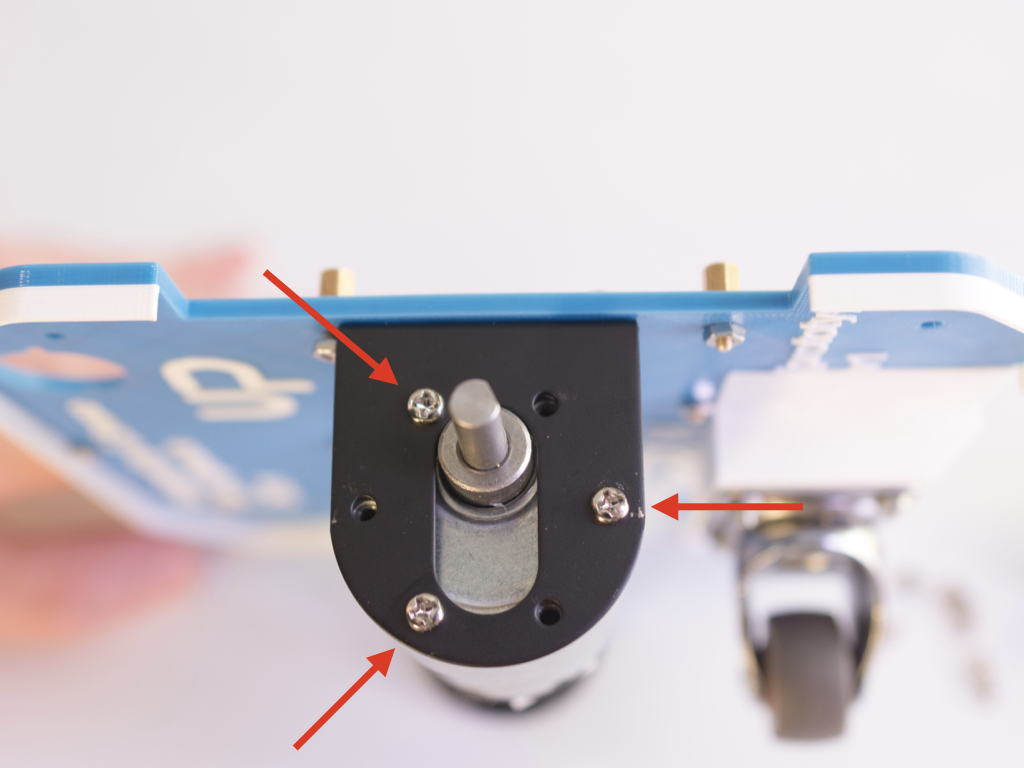
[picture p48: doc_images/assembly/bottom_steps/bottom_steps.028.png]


26. Now complete the motor by using other 3 screws

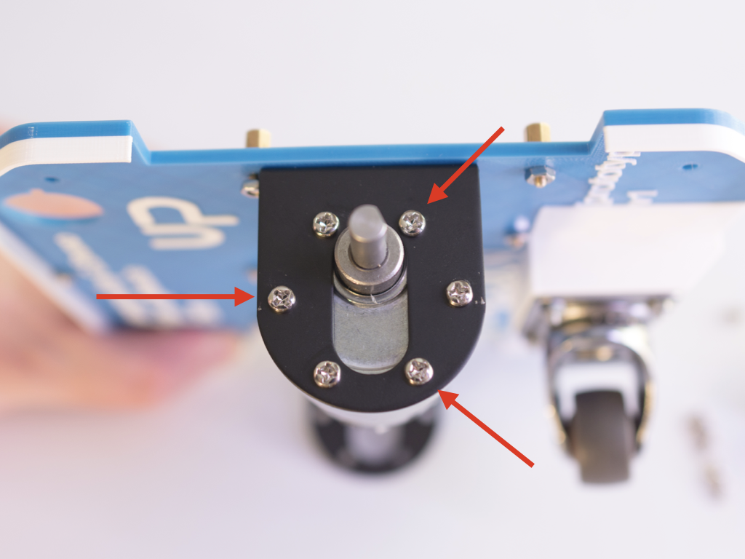
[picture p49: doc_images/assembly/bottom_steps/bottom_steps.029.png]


27. Mount the other motor, too

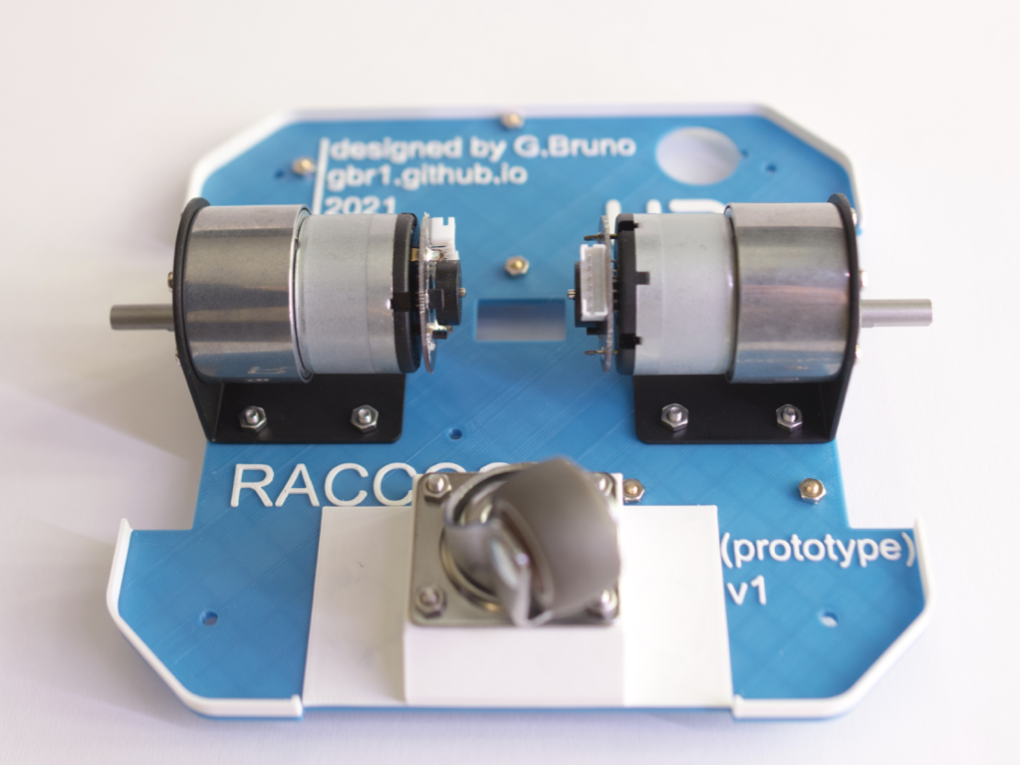
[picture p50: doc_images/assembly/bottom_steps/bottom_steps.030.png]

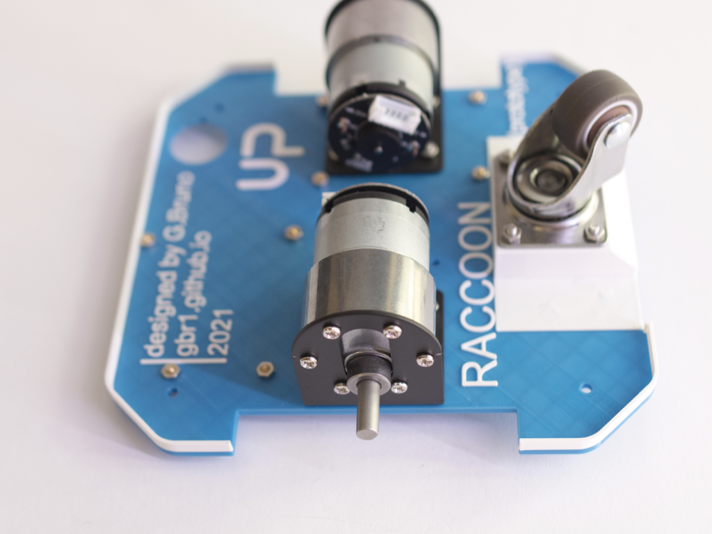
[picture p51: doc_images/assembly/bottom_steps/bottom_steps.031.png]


28. Bring the Moebiustech SMT32 board (you need to flash the firmware) and 4 M2.5x4 screws



29. Mount and fix using screws. Please check if it is aligned with the standoff

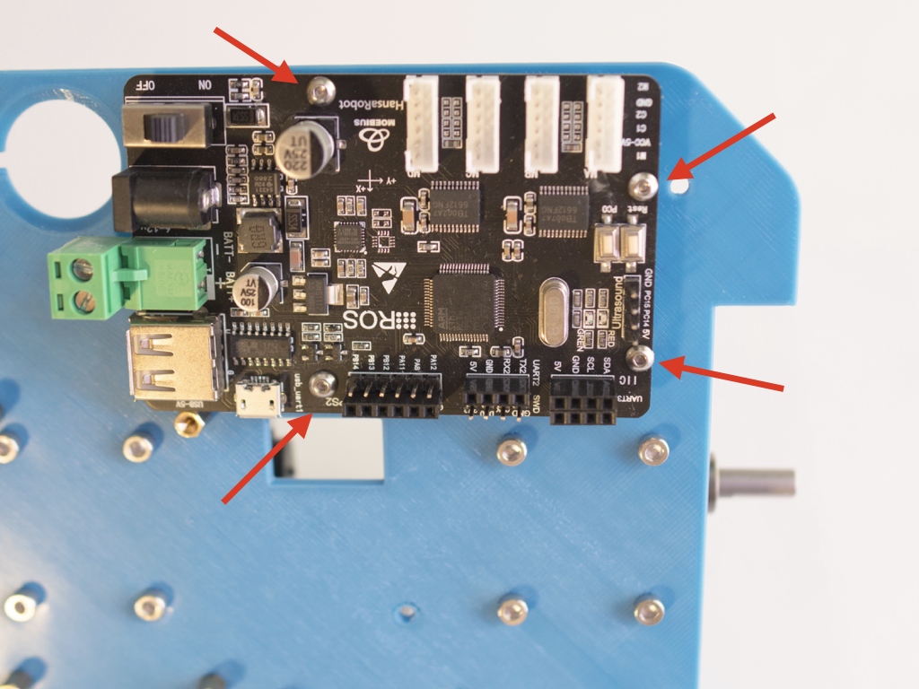
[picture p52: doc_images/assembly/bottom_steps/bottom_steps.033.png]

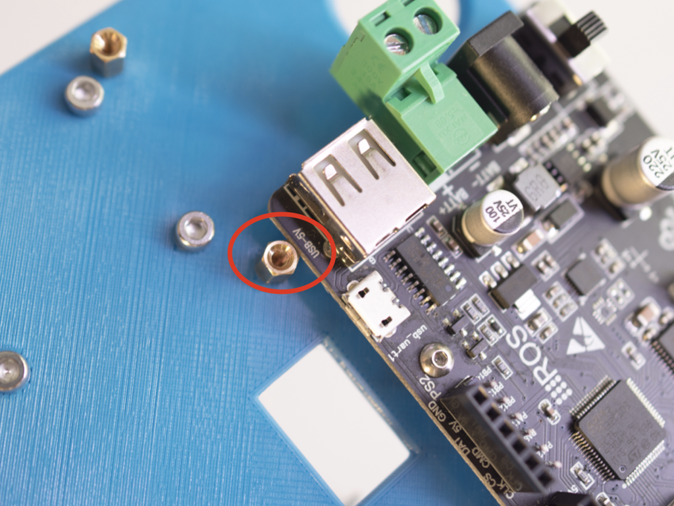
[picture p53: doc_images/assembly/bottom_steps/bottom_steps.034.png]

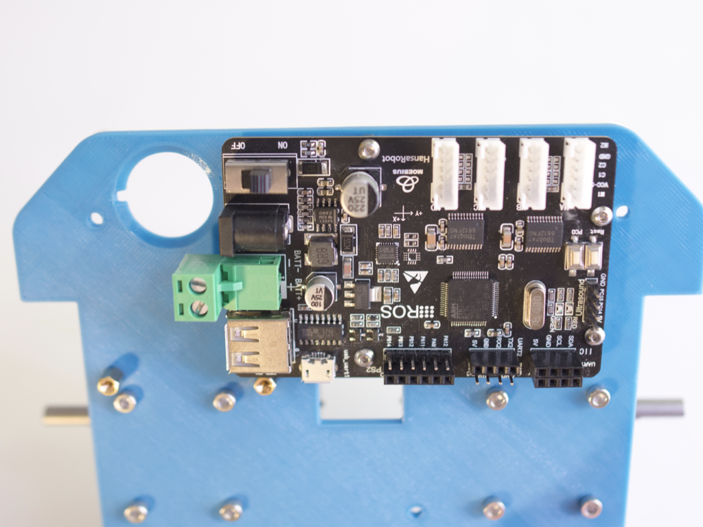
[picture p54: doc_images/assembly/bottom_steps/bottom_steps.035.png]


30. Now get the DCDC converter and 4 M2.5x4 screws



31. Mount as shown (led is on the back of the robot)



32. Now you need the power button



33. Mount from the bottom side, check the guide





34. Bring a M3x10 screw and an electrical screwed connector



35. Insert the screw from the bottom as shown



36. Mount the component on the top side



37. Now you need a DEANS cable and a 20cm white cable



38. Fix the two cables into the 2 parallel slots of the connector (check no shortcut)



39. Connect the red cable from the power switch to the red one of DEANS cable



40. Connect the white cable to the black one of DEANS cable



41. Now you need a cyan cable and a purple one



42. Fix the cyan and the white cable on the Moebiustech board negative (-) pole



43. Connect the black and the purple wire to positve (+) of Moebiustech board



44. Connect the purple cable to the input positive (+) of DCDC and the cyan to the negative input (-)



45. Bring the jack cable



46. Connect to the output of the DCDC, red is positive (+) and the black is negative (-)



47. For next steps you need 2 motor cables



48. Attach one cable for motor



49. Pass cables in the central slot



50. Attach the left motor to MOTOR D (left is viewing the robot from topand with the board on front)



51. Attach the right motor to MOTOR C



52. Now you need an usb micro cable



53. Plug the cable into the Moebiustech board



54. Pick 2 wheels



55. Mount wheels by screwing the hexagonal headed grain



56. Following photos shows the final result




57. Bring 4 M3x30 standoffs and 4 M3 nuts



58. Mount the standoffs as shown




59. Now you need a voltmeter and a 3S LiPo battery. In following steps you will calibrate the DCDC buck converter



60. Connect the battery



61. Press the button on bottom



62. Check that board is turned on and red light is turned on



63. Measure voltage on the jack (central is positive)



64. Screw the tiny potenziometer until voltmeter shows something between 5V and 5.1V




65. Turn off by pressing the bottom switch and detach the battery



66. The bottom plate is ready




> ***Copyright © 2021 G. Bruno gbr1.github.io under MIT license***

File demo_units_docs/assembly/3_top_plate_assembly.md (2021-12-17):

# Top plate setup

1. Bring the 3d printed top plate, a D435i camera, 2 M3x10 screws and 2 M3 washers



2. Remove the USB cap from the Intel Realsense camera



3. Screw the camera by using the screws and the washers



4. This is how it should be.



5. Now, bring the UP Squared you have already prepared and 4 M2.5x6 screws



6. Mount the UP Squared on the top plate



7. Pass to the bottom side antennas cables



7. Mount the antenna and screw using the washer and the nut



8. Glue the antenna using the adesive



9. Bring the joypad usb, a usb cable and a cable tie



10. Insert the joypad usb into the frontal usb port



11. Insert the usb cable into the Realsense camera



12. Insert the usb of the camera into one of the back usb port



13. Using the cable tie organize the cable



14. Pull the cable tie to make the cable fixed



15. Cut the remaining part of the cable tie



16. Bring the antenna



17. Screw the antenna



18. The top plate is ready!!!

> ***Copyright © 2021 G. Bruno gbr1.github.io under MIT license***

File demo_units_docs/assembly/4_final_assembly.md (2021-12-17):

# Final assembly

1.  You need the two parts and 4 M3x8 screws



2.  Mount the top part using the screws. Remember that camera and board must be aligned (it is the front)



3.  Pass the usb cable from bottom to top and plug the usb connector on the back of UP Squared



4.  Connect the jack into power input of UP Squared



5.  Inser battery



6.  Plug the DEANS connector



7.  Attach the magnetic holder



8.  Remove the protection from D435i



9.  Your Raccoon robot is ready to use!



> ***Copyright © 2021 G. Bruno gbr1.github.io under MIT license***

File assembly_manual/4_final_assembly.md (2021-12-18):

# Final assembly

# 

## 1. List of components required for next steps

- Bottom part of the robot

- Top part of the robot

- 4 M3x10 screws (*code M08*)

- 4 M3 nuts (*code M04*)

- USB 3.0 <-> USB C cable (*code E12*)

- USB 2.0 <-> micro USB (*code E13*)

- cable tie (*code M09*)

## 2. Mount the robot

1. Follow the video to mount the top section.

https://user-images.githubusercontent.com/9216366/146622010-1dc93084-384e-4ae7-ab8b-33d4da34a152.mp4

2. Plug the USB C cable (*code E12*) to the Intel Realsense and the USB 3.0 on the back of the robot. Fix the cable using the cable tie (*code M09*).

3. Pass the usb cable from bottom to top and plug the usb connector on the back of UP Squared



4. Connect the jack into power input of UP Squared



## 3. Battery

1. Insert the battery (3S LiPo)



2. Plug the DEANS connector



## 4. Optional - Battery holder

1. Insert magnets into the piece taking care of the polarity, the piece must be attracted by the bottom plate



2. Magnetically attach the holder



## Finish!

Your UP Raccoon is ready!



---

## Go to the software

Follow the [robot setup](../Raccoon%20robot%20setup.md) to start using your robot

---

> ***Copyright © 2021 G. Bruno gbr1.github.io under MIT license***

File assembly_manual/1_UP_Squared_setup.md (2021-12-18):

# UP Squared setup

# 

## 1. List of the component needed in following steps

- UP Squared (*code E01*)

- WiFi kit with antennas (*code E02*)

- AI Core X kit (*code E03*)

- 4x M2.5x20+6 standoffs (*code M01*), you can also build from smaller if you haven't got them

- 4x M2.5 nuts (*code M03*)



## 2. Prepare the UP Squared

1. You have to replace heatsink with standoffs 



2. Screw a nut on a standoff and replace the UP Squared screw. Continue in cross like in following photos






3. Bring the AI Core X kit and mount the module in the PCI-e socket



4. Fix the module sing the included screw



5. Bring the WiFi kit and insert in the M2 socket



6. Fix the WiFi card using the included screw



7. Bring the flexible PCB antenna and connect on port 2 of WiFi card



8. Mount the other antenna cable (SMA) on port 1 of WiFi card



9. Your UP Squared is ready to be mounted.

---

## 3. Next step

[Go to the bottom plate assembly guide](2_bottom_plate_setup.md)

---

> ***Copyright © 2021 G. Bruno gbr1.github.io under MIT license***

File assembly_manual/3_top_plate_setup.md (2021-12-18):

# Top plate setup

# 

## 1. List of components required for this section

- Top plate (*code P02*)

- UP Squared, previously configured

- Intel Realsense D435/D435i (*code E02*)

- SMA WiFi antenna (*code E03*)

- 2x M3x10 screws (*code M08*)

## 2. Assemble

Follow the video to mount the top section.

https://user-images.githubusercontent.com/9216366/146613192-e322e2f5-3453-4d04-a1d4-09b31b742257.mp4

---

## 3. Next Step

[Go to the final assembly](4_final_assembly.md)

---

> ***Copyright © 2021 G. Bruno gbr1.github.io under MIT license***

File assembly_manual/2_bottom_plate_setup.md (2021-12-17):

# Bottom plate setup

# 

## 1. List of the component needed in following steps

- Bottom plate (*code P01*)

- Moebiustech spacer (*code P04*)

- DCDC spacer (*code P05*)

- 4x M2.5 nuts (*code M03*)

- 8x M3 nuts (*code M04*)

- 14x M2.5x6 screws (*code M05*)

- 4x M2.5x14 screws (*code M06*)

- 12x M3x5 screws (*code M07*)

- 10x M3x10 screws (*code M08*)

- 2x Gearmotor brackets (*code M10*)

- 2x Wheels (*code M11*)

- 2x Magnets ⌀10x3 (*code M12*)

- Caster wheel (*code M13*)

- Moebiustech STM32 board (*code E04*)

- DCDC (*code E05*)

- 2x Gearmotor (*code E07*)

- 2x gearmotor cable (*code E08*)

- Power switch with cable (*code E09*)

- Power jack with cable (*code E10*)

- 22AWG cable (*code E11*)

- DEANS cable (*code E14*)

- Mammouth connector (*code E15*)

## 2. Mounting the bottom of the robot

Follow the video to mount the bottom section.

https://user-images.githubusercontent.com/9216366/146599040-81ecf0cd-299c-41ea-be90-967f67150cd5.mp4

## 3. Wiring

Following diagram shows how to wire the bottom section of the robot.



*Note: You can use longer cables*

Animation of the wiring

https://user-images.githubusercontent.com/9216366/146600231-4f52fe80-296f-4ad2-b1c7-9e365fd438a7.mp4

## 4. Calibrate the power stage

1. Now you need a voltmeter and a 3S LiPo battery. In following steps you will calibrate the DCDC buck converter



2. Connect the battery



3. Press the switch on the bottom of the robot to turn on (symbol **I**)



4. Check that board is turned on and red light is turned on, if not check the switch on the board that is setted on **ON**.



5. Measure voltage on the jack (central is positive)



6. Screw the tiny potenziometer until voltmeter shows something between 5V and 5.1V




7. You have just calibrated the power stage. Turn off by pressing the bottom switch and detach the battery.



---

## 5. Next step

[Go to the top plate building](3_top_plate_setup.md)

---

> ***Copyright © 2021 G. Bruno gbr1.github.io under MIT license***

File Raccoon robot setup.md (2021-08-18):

# Raccoon robot setup

---

> In this section you will guided on how to setup your robot in the following phases:
> 
> 1. OS installation
> 
> 2. Realsense setup
> 
> 3. ROS installation
> 
> 4. OpenVINO installation
> 
> 5. ROS packages setup
> 
> 6. Demo setup

---

## 1.  OS Installation

For this part you can follow: [Ubuntu_20.04 · up-board/up-community Wiki · GitHub](https://github.com/up-board/up-community/wiki/Ubuntu_20.04)

Steps to do are also described here.

- Download Ubuntu 20.04.2 from the official website and put on a pen drive using balena etcher.
  Plug the bootable pendrive into your UP Squared and turn on.

- Follow the instruction by doing a *minimal installation*

*NOTE: if you want to setup like the demo robot use "robot" as username and "demo" as computer name. Password is "demo". Set "log in automatically".*

- After installed Ubuntu, you need to patch the kernel using the UP ppa. Open the terminal and type:

```bash
sudo add-apt-repository ppa:aaeon-cm/5.4-upboard
sudo apt update
```

Remove all the generic installed kernel (select No on the question "Abort Kernel Removal")

```bash
sudo apt-get autoremove --purge 'linux-.*generic'
sudo apt-get install linux-generic-hwe-18.04-5.4-upboard
sudo apt dist-upgrade -y
sudo update-grub
sudo reboot
```

After reboot check the kernel:

```bash
uname -a
```

result must be:

```bash
Linux demo 5.4.0-1-generic #2~upboard2-Ubuntu SMP Thu Jul 25 13:35:27 UTC 2019 x86_64 x86_64 x86_64 GNU/Linux
```

Now we need to install the upboard-extras

```bash
sudo apt install upboard-extras
sudo usermod -a -G gpio ${USER}
sudo usermod -a -G leds ${USER}
sudo usermod -a -G spi ${USER}
sudo usermod -a -G i2c ${USER}
sudo usermod -a -G dialout ${USER}
sudo reboot
```

Now you are ready for step 2.

## 2.  Realsense setup

We need to install linux headers.

```bash
sudo apt install linux-headers-5.4.0-1-generic
sudo ln -s /usr/src/linux-headers-5.4.0-1-generic/ /lib/modules/5.4.0-1-generic/build
```

Now install the librealsense and realsense packages.

```bash
sudo apt-key adv --keyserver keyserver.ubuntu.com --recv-key F6E65AC044F831AC80A06380C8B3A55A6F3EFCDE || sudo apt-key adv --keyserver hkp://keyserver.ubuntu.com:80 --recv-key F6E65AC044F831AC80A06380C8B3A55A6F3EFCDE
sudo add-apt-repository "deb https://librealsense.intel.com/Debian/apt-repo $(lsb_release -cs) main" -u
sudo apt-get install librealsense2-dkms
sudo apt-get install librealsense2-utils
sudo apt-get install librealsense2-dev
sudo apt-get install librealsense2-dbg
```

then check if kernel is updated by:

`modinfo uvcvideo | grep "version:"`

result must include `realsense`

Then type `realsense-viewer` and update your RealSense camera if needed.

You can proceed to ROS installation.

## 3.  ROS installation

You can follow this guide: [noetic/Installation/Ubuntu - ROS Wiki](http://wiki.ros.org/noetic/Installation/Ubuntu)[noetic/Installation/Ubuntu - ROS Wiki](http://wiki.ros.org/noetic/Installation/Ubuntu)

```bash
sudo sh -c 'echo "deb http://packages.ros.org/ros/ubuntu $(lsb_release -sc) main" > /etc/apt/sources.list.d/ros-latest.list'
sudo apt install curl
curl -s https://raw.githubusercontent.com/ros/rosdistro/master/ros.asc | sudo apt-key add -
sudo apt update
sudo apt install ros-noetic-desktop-full
echo "source /opt/ros/noetic/setup.bash" >> ~/.bashrc
source ~/.bashrc
sudo apt install python3-rosdep python3-rosinstall python3-rosinstall-generator python3-wstool build-essential
sudo apt install python3-rosdep
sudo rosdep init
rosdep update
mkdir -p ~/catkin_ws/src
cd ~/catkin_ws/
catkin_make
echo "source ~/catkin_ws/devel/setup.bash" >> ~/.bashrc
source ~/.bashrc
```

You can now proceed to OpenVINO installation

## 4.  OpenVINO installation

Go to OpenVINO [website](https://docs.openvinotoolkit.org/latest/index.html) and download the release 2021.4 LTS.

Extract the folder l_openvino_toolkit_p_2021.4.582 on your Desktop folder.

```bash
cd ~/Desktop/l_openvino_toolkit_p_2021.4.582
sudo ./install_openvino_dependencies.sh
sudo ./install_GUI.sh
cd /opt/intel/openvino_2021/install_dependencies
sudo -E ./install_openvino_dependencies.sh
echo "source /opt/intel/openvino_2021/bin/setupvars.sh" >> ~/.bashrc
source ~/.bashrc
cd /opt/intel/openvino_2021/deployment_tools/model_optimizer/install_prerequisites
sudo ./install_prerequisites_caffe.sh
```

Now you need to install Myriad X support  (NCS2 or Ai Core X)

```bash
sudo usermod -a -G users "$(whoami)"
sudo cp /opt/intel/openvino_2021/inference_engine/external/97.myriad-usbboot.rules /etc/udev/rules.d
sudo udevadm control --reload-rules
sudo udevadm trigger
sudo ldconfig
sudo reboot
```

You have setted everything you need to start working with ROS packages and get your robot working!

## 5. ROS packages setup

You can start by installing dependencies:

```bash
sudo pip3 install tornado
sudo pip3 install simplejpeg
sudo apt install ros-noetic-realsense2-camera
```

Then you can clone repos:

```bash
cd ~/catkin_ws/src
git clone https://github.com/dheera/rosboard
git clone https://github.com/gbr1/moebiustech_stm32_ros
git clone https://github.com/gbr1/raccoon_ros
git clone -b new_core_api https://github.com/gbr1/ros_openvino
```

Now you need to install all the dependencies:

```bash
cd ..
rosdep install --from-paths src --ignore-src -r -y
catkin_make
catkin_make install
```

Your robot is ready to use!

If you want you can also configure the robot in "demo mode".

## 6.  Demo setup

You need to change permission to the startup script.

```bash
cd ~/catkin_ws/src/raccoon_ros/raccoon_demo/scripts/
chmod u+x startup.sh
```

Then in your launchpad search for "Startup application".

Inside set a new command called "demo" with the following command:

`gnome-terminal --command="/home/robot/catkin_ws/src/raccoon_ros/raccoon_demo/scripts/startup.sh"`

This will launch the demo at the startup.

Then you need to open the hotspot.

Go in Wi-Fi settings and "turn on hotspot" from 3 dots button.
Call the network "raccoon-robot" and set the password as "robotdemo".

Then edit to **true** the param **autoconnect** in following file:

`sudo -H gedit /etc/NetworkManager/system-connections/Hotspot.nmconnection`

You can now turn off the robot. When you turn the robot on, the demo will start and you will be able to connect to the robot hotspot.

The setup is ended.

> ***Copyright © 2021 G.Bruno gbr1.github.io under MIT license***

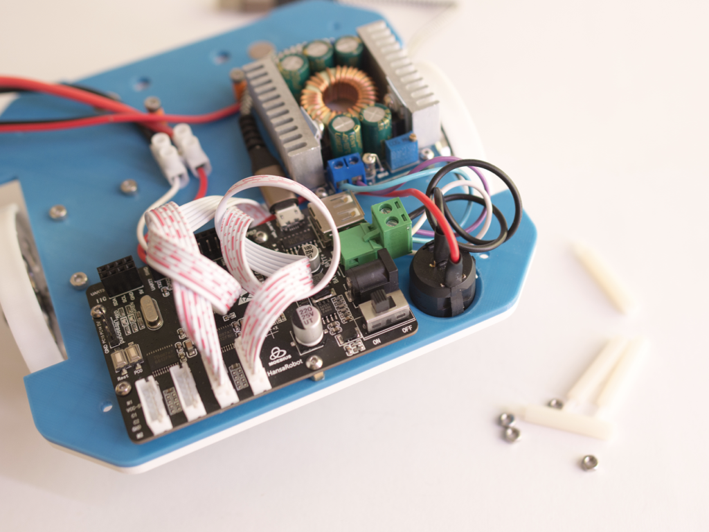
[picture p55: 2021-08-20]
doc_images/assembly/bottom_steps/bottom_steps.066.png

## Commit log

2021-12-17 update to rev2
    [battery_cover v3.step, battery_cover.stl, battery_cover_demo.stl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]
2021-12-18 added legacy files
    [adapter v1.stl, battery_cover_edukit_demo v4.stl, battery_screw v1.stl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]
